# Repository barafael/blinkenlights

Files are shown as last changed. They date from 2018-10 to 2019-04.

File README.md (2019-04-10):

# blinkenlights: Blink lights and control other things, controlled by up to 5 input channels

The purpose of this board is to read some standard RC PWM channels, and switch the output MOSFETs accordingly.
This can be used to blink lights on an RC airplane in patterns, for example. The input channel allows to switch between modes, like standard flying mode and Taxi/Standby modes. Or, a landing light can be switched on/off by a separate channel.
The channels can be either dedicated lines from the receiver, or just other lines which are in use anyway. For example, the throttle signal could be used to switch between standby and flying, and the landing flaps signal could turn on/off the landing lights.

It would be easily possible to dim lights using PWM, I just have not made use of that yet.

The code pretty much just reads the input channels and reads the state from them, and then passes that state (and a tick value) to a function for each output pin. The function can then decide to do whatever with the output pin.

RC PWM signal is read using interrupts, and the program detects when a signal has been disconnected, resetting the state accordingly. That means that you can attach, detach, and reattach PWM signals during operation as you like.

The I2C pins are still free and accessible, so it would be possible to hook up I2C sensors also, like a temperature sensor on the brakes or a barometer.

Input voltage goes directly to the Pro Mini internal regulator, that means it should be 3.3V-16V.

That input voltage is directly supplied to the output pins via the MOSFET driver: an IRLML6244TRPBF SOT-23 package which can switch up to 6.3A (according to datasheet, but I haven't stressed it like that yet).

The PCB is designed in KiCad.

If you have any suggestions or spot an error somewhere, please let me know!

Render of PCB:
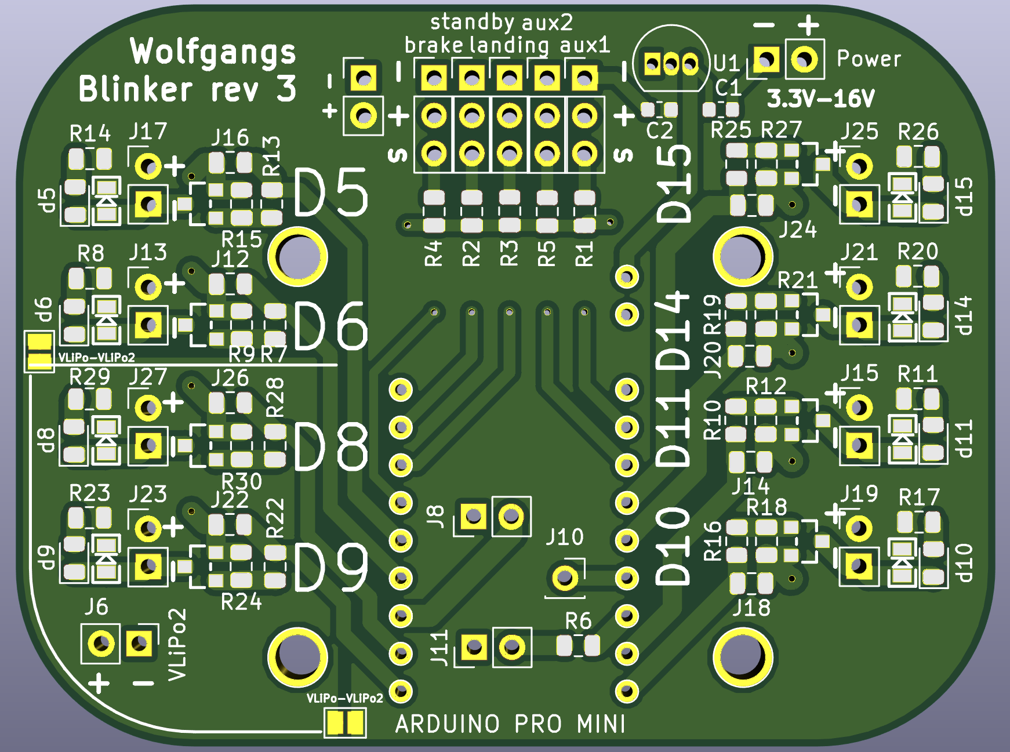
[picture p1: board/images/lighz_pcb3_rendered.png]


PCB in pcbnew:
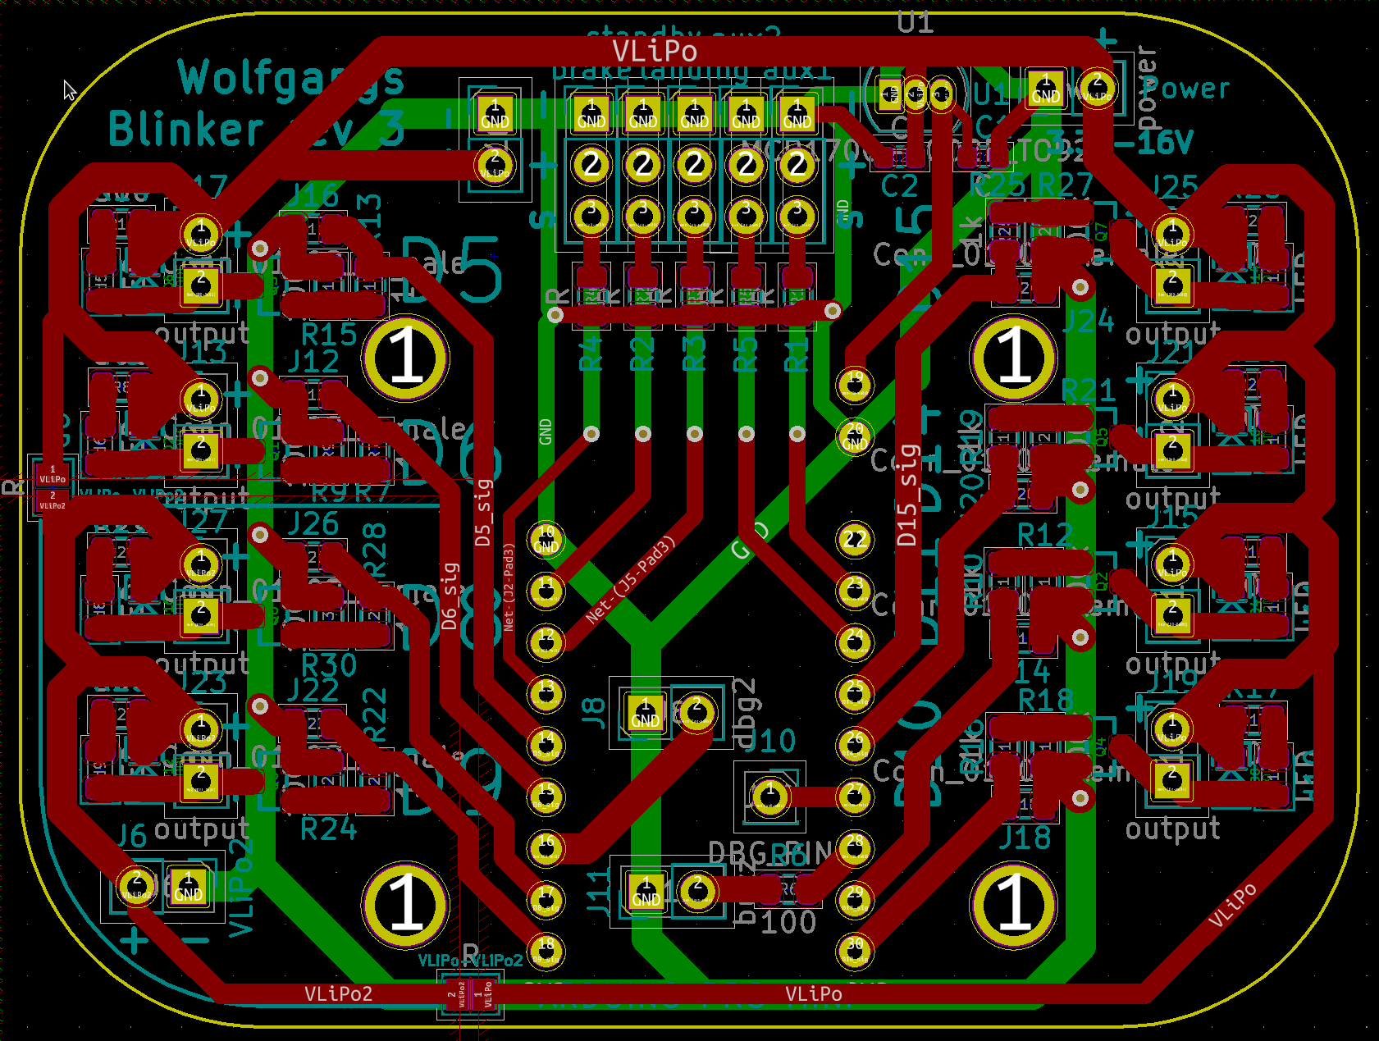
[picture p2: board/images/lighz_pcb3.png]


Schematic:
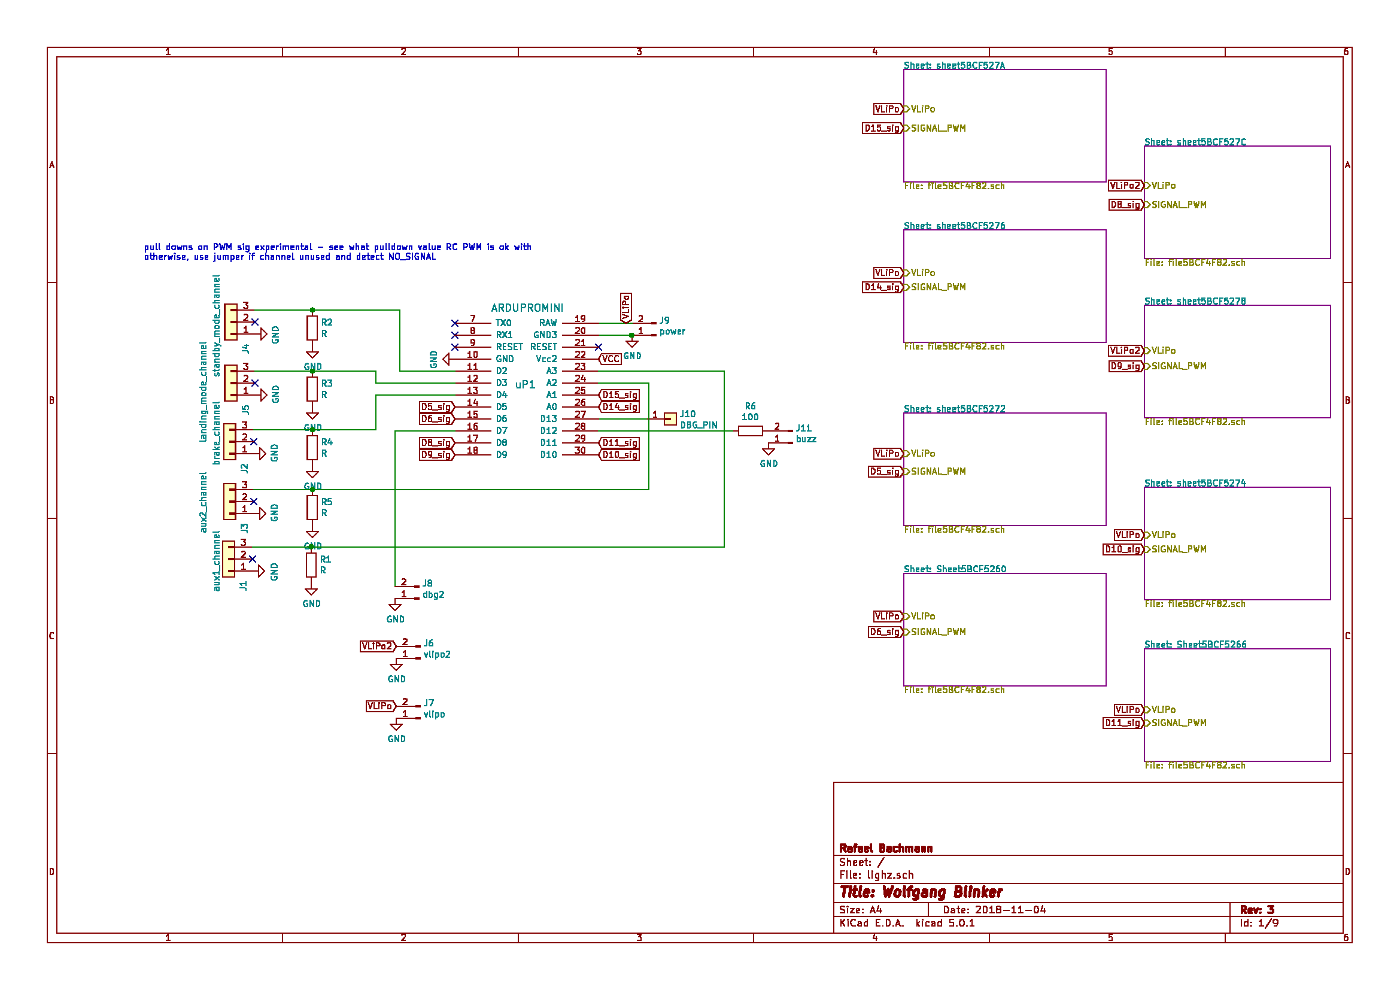
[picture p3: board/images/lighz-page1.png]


MOSFET driver schematic:
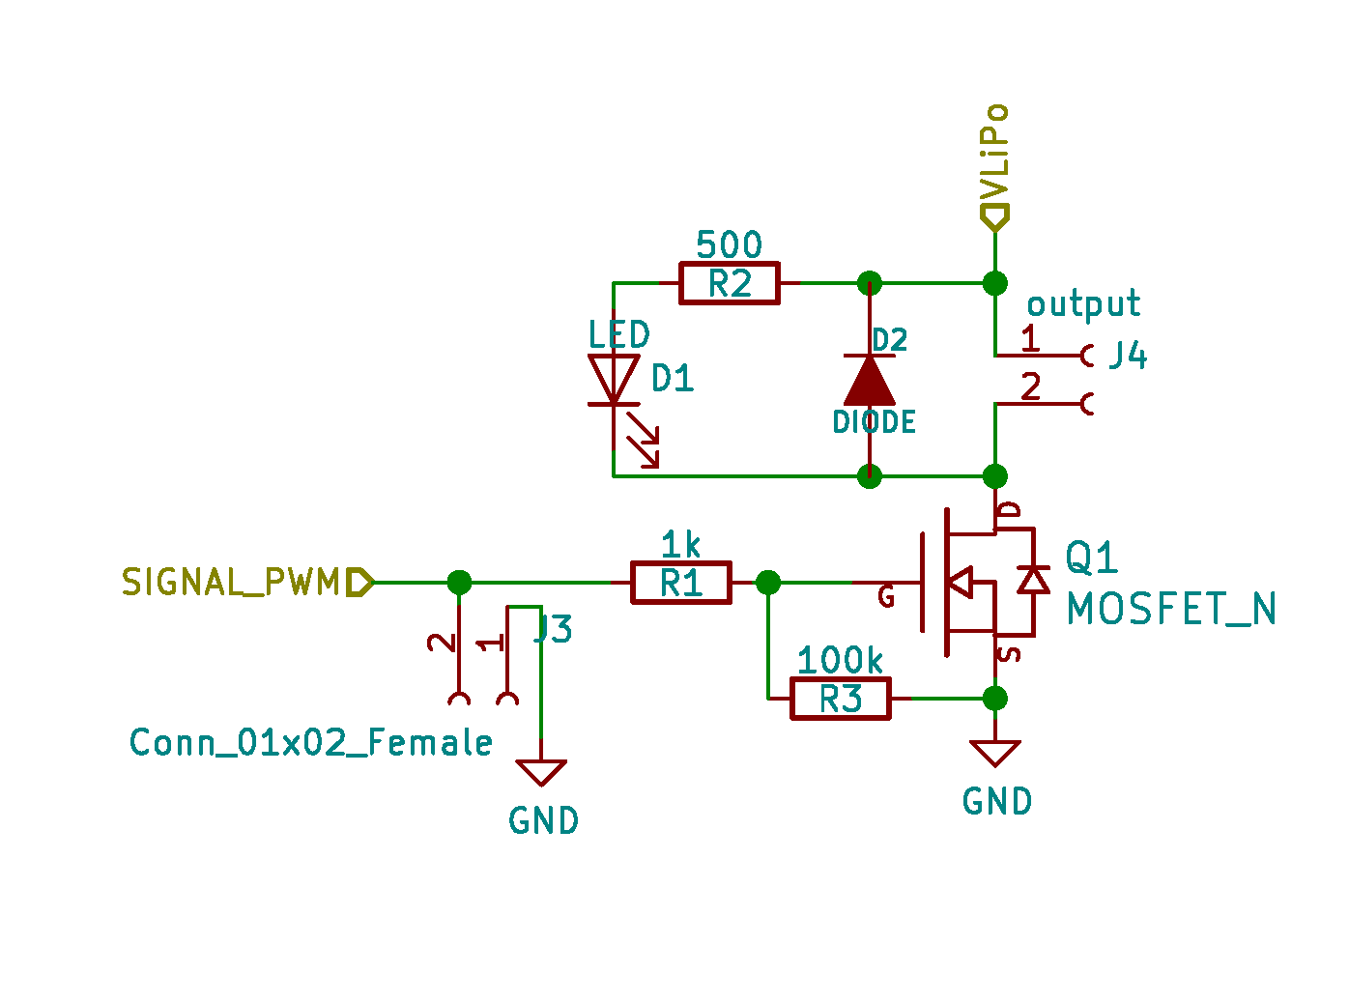
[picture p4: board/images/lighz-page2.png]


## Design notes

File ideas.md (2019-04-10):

stm32f030 board. Run RTOS, threads for each lamp.

each pin has config slot. Config board is extra thing that you can plug in config slot.
Configures:
* N modes: you can select which mode to apply settings to (standby, flying, etc)
* led intensity: PWM value, +/- buttons, 7seg displ?
* pattern button: activate (push down), play pattern on other button, deactivate (release)
* speed: how many seconds per run
* ...

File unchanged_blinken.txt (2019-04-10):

#include <PinChangeInterrupt.h>
#include <PinChangeInterruptBoards.h>
#include <PinChangeInterruptPins.h>
#include <PinChangeInterruptSettings.h>

#include <DigitalIO.h>

static DigitalPin<13> TEST_PIN;

static DigitalPin<5>  D5_PIN;
static DigitalPin<6>  D6_PIN;
static DigitalPin<8>  D8_PIN;
static DigitalPin<9>  D9_PIN;
static DigitalPin<10> D10_PIN;
//static DigitalPin<11> D11_PIN;
static DigitalPin<14> D14_PIN;
static DigitalPin<15> D15_PIN;

static const int BUZZER_PIN = 12;

static DigitalPin<7> DBG_PIN;

/* To enter standby mode, activate landing lights, or enable brakes etc.
   apply an RC PWM signal to these pins */
// Only 2, 3 pins support real interrupts on the pro mini
static const int STANDBY_MODE_CHANNEL_PIN  = 2;
static const int LANDING_LIGHT_CHANNEL_PIN = 3;
static const int BRAKE_CHANNEL_PIN         = 4;
static const int AUX1_CHANNEL_PIN          = A3;
static const int AUX2_CHANNEL_PIN          = A2;

/* These thresholds define when a mode should be active
   (compared against RC PWM value on resp. pin) */
static const uint64_t STANDBY_MODE_THRESHOLD  = 1900;
static const uint64_t LANDING_LIGHT_THRESHOLD = 1800;
static const uint64_t BRAKE_THRESHOLD         = 1500;

/* Counter for main loop,
   subdivides each cycle into MILLISECONDS_PER_CYCLE steps */
static uint64_t counter = 0;

/* The counter runs 0..COUNTER_MAX */
static const uint64_t COUNTER_MAX = 1000;

/* loop wait time MILLISECONDS_PER_STEP is such that one entire counter cycle
   takes MILLISECONDS_PER_CYCLE milliseconds */
static const uint64_t MILLISECONDS_PER_CYCLE = 1200;
static const uint64_t MILLISECONDS_PER_STEP  = MILLISECONDS_PER_CYCLE / COUNTER_MAX;

typedef enum { FLYING, STANDBY } mode_t;

typedef struct {
  mode_t mode;
  /* Flag indicates if landing light should be on */
  bool landing_light_active;
  bool brake_active;
} state_t;

static state_t current_state = { FLYING, false, false };

/* Time in microseconds after which an RC PWM signal is considered stale */
#define PWM_CYCLE_TIMEOUT_MICROS 20000
#define PWM_PULSE_TIMEOUT_MICROS 5000

/* Flag invalid RC PWM pulse signal */
static const uint8_t NO_SIGNAL = 0;

/* Variables to measure pulse duration of RC PWM pulse
   volatile because shared with interrupts */
static volatile uint64_t standby_channel_rise_shared;
static volatile uint64_t standby_channel_pulse_time_shared;

static volatile uint64_t landing_channel_rise_shared;
static volatile uint64_t landing_channel_pulse_time_shared;

static volatile uint64_t brake_channel_rise_shared;
static volatile uint64_t brake_channel_pulse_time_shared;

static volatile uint64_t aux1_channel_rise_shared;
static volatile uint64_t aux1_channel_pulse_time_shared;

static volatile uint64_t aux2_channel_rise_shared;
static volatile uint64_t aux2_channel_pulse_time_shared;

/* Non-volatile, non-shared variables to access pulse time */
static uint64_t standby_channel_pulse_time = NO_SIGNAL;
static uint64_t landing_channel_pulse_time = NO_SIGNAL;
static uint64_t brake_channel_pulse_time   = NO_SIGNAL;
static uint64_t aux1_channel_pulse_time    = NO_SIGNAL;
static uint64_t aux2_channel_pulse_time    = NO_SIGNAL;

static uint64_t standby_channel_rise;
static uint64_t landing_channel_rise;
static uint64_t brake_channel_rise;
static uint64_t aux1_channel_rise;
static uint64_t aux2_channel_rise;

void setup() {
  Serial.begin(250000);

  TEST_PIN.mode(OUTPUT);

  D5_PIN.mode(OUTPUT);
  D6_PIN.mode(OUTPUT);
  D8_PIN.mode(OUTPUT);
  D9_PIN.mode(OUTPUT);
  D10_PIN.mode(OUTPUT);
  //D11_PIN.mode(OUTPUT);
  pinMode(11, OUTPUT);
  D14_PIN.mode(OUTPUT);
  D15_PIN.mode(OUTPUT);

  /* Turn off the lights */
  TEST_PIN.low();

  D5_PIN.low();
  analogWrite(6, 0);
  D8_PIN.low();
  D9_PIN.low();
  analogWrite(10, 0);
  //D11_PIN.low();
  D14_PIN.low();
  D15_PIN.low();

  pinMode(STANDBY_MODE_CHANNEL_PIN,  INPUT);
  pinMode(LANDING_LIGHT_CHANNEL_PIN, INPUT);
  pinMode(BRAKE_CHANNEL_PIN,         INPUT);
  pinMode(AUX1_CHANNEL_PIN,          INPUT);
  pinMode(AUX2_CHANNEL_PIN,          INPUT);

  /* Attach interrupts for pulse time measurement */
  attachInterrupt(digitalPinToInterrupt(STANDBY_MODE_CHANNEL_PIN),  standby_channel_interrupt, CHANGE);
  attachInterrupt(digitalPinToInterrupt(LANDING_LIGHT_CHANNEL_PIN), landing_channel_interrupt, CHANGE);

  /* Use PinChangeInterrupt for pins other than 2, 3 */
  attachPinChangeInterrupt(digitalPinToPinChangeInterrupt(BRAKE_CHANNEL_PIN), brake_channel_interrupt, CHANGE);
  attachPinChangeInterrupt(digitalPinToPinChangeInterrupt(AUX1_CHANNEL_PIN),  aux1_channel_interrupt,  CHANGE);
  attachPinChangeInterrupt(digitalPinToPinChangeInterrupt(AUX2_CHANNEL_PIN),  aux2_channel_interrupt,  CHANGE);

  startup_blink();
  startup_buzz();
}

void startup_blink() {
  TEST_PIN.high();
  delay(50);
  D5_PIN.high();
  delay(50);
  analogWrite(6, 100);
  delay(50);
  D8_PIN.high();
  delay(50);
  D9_PIN.high();
  delay(50);
  analogWrite(10, 100);
  delay(50);
  //D11_PIN.high();
  delay(50);
  D14_PIN.high();
  delay(50);
  D15_PIN.high();
  delay(50);

  TEST_PIN.low();
  D5_PIN.low();
  analogWrite(6, 0);
  D8_PIN.low();
  D9_PIN.low();
  analogWrite(10, 0);
  //D11_PIN.low();
  D14_PIN.low();
  D15_PIN.low();
}

void startup_buzz() {
  tone(BUZZER_PIN, 1245);
  delay(100);
  noTone(BUZZER_PIN);
  tone(BUZZER_PIN, 1319);
  delay(100);
  noTone(BUZZER_PIN);
  tone(BUZZER_PIN, 1568);
  delay(100);
  noTone(BUZZER_PIN);
  tone(BUZZER_PIN, 1976);
  delay(100);
  noTone(BUZZER_PIN);
  tone(BUZZER_PIN, 2349);
  delay(200);
  noTone(BUZZER_PIN);
  tone(BUZZER_PIN, 2093);
  delay(100);
  noTone(BUZZER_PIN);
  tone(BUZZER_PIN, 1568);
  delay(200);
  noTone(BUZZER_PIN);
  tone(BUZZER_PIN, 1319);
  delay(100);
  noTone(BUZZER_PIN);
  tone(BUZZER_PIN, 2349);
  delay(200);
  noTone(BUZZER_PIN);
  tone(BUZZER_PIN, 2093);
  delay(400);
  noTone(BUZZER_PIN);
}

void loop() {
  uint64_t loop_start_millis = millis();

  /* Handle RC PWM input */
  {
    /* Copy over shared volatile variables */
    noInterrupts();
    standby_channel_pulse_time = standby_channel_pulse_time_shared;
    landing_channel_pulse_time = landing_channel_pulse_time_shared;
    brake_channel_pulse_time   = brake_channel_pulse_time_shared;
    aux1_channel_pulse_time    = aux1_channel_pulse_time_shared;
    aux2_channel_pulse_time    = aux2_channel_pulse_time_shared;

    standby_channel_rise = standby_channel_rise_shared;
    landing_channel_rise = landing_channel_rise_shared;
    brake_channel_rise   = brake_channel_rise_shared;
    aux1_channel_rise    = aux1_channel_rise_shared;
    aux2_channel_rise    = aux2_channel_rise_shared;
    interrupts();

    /* Check for stale pulse time readings */
    const uint64_t now = micros();
    if ((now - standby_channel_rise) > PWM_CYCLE_TIMEOUT_MICROS ||
        standby_channel_pulse_time > PWM_PULSE_TIMEOUT_MICROS) {
      // ignoring interrupt here, assumption is that it won't been triggered
      // since that has not happened for PWM_CYCLE_TIMEOUT_MICROS microseconds
      standby_channel_pulse_time        = NO_SIGNAL;
      standby_channel_pulse_time_shared = NO_SIGNAL;
    }
    if ((now - landing_channel_rise) > PWM_CYCLE_TIMEOUT_MICROS ||
        landing_channel_pulse_time > PWM_PULSE_TIMEOUT_MICROS) {
      // ignoring interrupt here, assumption is that it won't been triggered
      // since that has not happened for PWM_CYCLE_TIMEOUT_MICROS microseconds
      landing_channel_pulse_time        = NO_SIGNAL;
      landing_channel_pulse_time_shared = NO_SIGNAL;
    }
    if ((now - brake_channel_rise) > PWM_CYCLE_TIMEOUT_MICROS ||
        brake_channel_pulse_time > PWM_PULSE_TIMEOUT_MICROS) {
      // ignoring interrupt here, assumption is that it won't been triggered
      // since that has not happened for PWM_CYCLE_TIMEOUT_MICROS microseconds
      brake_channel_pulse_time        = NO_SIGNAL;
      brake_channel_pulse_time_shared = NO_SIGNAL;
    }
    if ((now - aux1_channel_rise) > PWM_CYCLE_TIMEOUT_MICROS ||
        aux1_channel_pulse_time > PWM_PULSE_TIMEOUT_MICROS) {
      // ignoring interrupt here, assumption is that it won't been triggered
      // since that has not happened for PWM_CYCLE_TIMEOUT_MICROS microseconds
      aux1_channel_pulse_time        = NO_SIGNAL;
      aux1_channel_pulse_time_shared = NO_SIGNAL;
    }
    if ((now - aux2_channel_rise) > PWM_CYCLE_TIMEOUT_MICROS ||
        aux2_channel_pulse_time > PWM_PULSE_TIMEOUT_MICROS) {
      // ignoring interrupt here, assumption is that it won't been triggered
      // since that has not happened for PWM_CYCLE_TIMEOUT_MICROS microseconds
      aux2_channel_pulse_time        = NO_SIGNAL;
      aux2_channel_pulse_time_shared = NO_SIGNAL;
    }
  }

  /* Read if signal present */
  bool standby_mode_enabled  = standby_channel_pulse_time != NO_SIGNAL;
  bool landing_light_enabled = landing_channel_pulse_time != NO_SIGNAL;

  /* Set mode to standby only if mode is enabled */
  if (standby_mode_enabled) {
    if (standby_channel_pulse_time < STANDBY_MODE_THRESHOLD) {
      current_state.mode = STANDBY;
    } else {
      current_state.mode = FLYING;
    }
  } else {
    /* If mode not enabled, state is FLYING */
    current_state.mode = FLYING;
  }

  if (landing_light_enabled) {
    current_state.landing_light_active = landing_channel_pulse_time < LANDING_LIGHT_THRESHOLD;
  } else {
    current_state.landing_light_active = false;
  }

  if (brake_channel_pulse_time > BRAKE_THRESHOLD) {
    current_state.brake_active = true;
  } else {
    current_state.brake_active = false;
  }

  /* Update outputs with current state */
  update_test_pin(counter, &current_state);

  updateOutput_D5(counter,  &current_state);
  updateOutput_D6(counter,  &current_state);
  updateOutput_D8(counter,  &current_state);
  updateOutput_D9(counter,  &current_state);
  updateOutput_D10(counter, &current_state);
  updateOutput_D11(counter, &current_state);
  updateOutput_D14(counter, &current_state);
  updateOutput_D15(counter, &current_state);

  /* Advance counter */
  if (counter < COUNTER_MAX) {
    counter++;
  } else {
    counter = 0;
  }

  //#define DEBUG_PRINT
#ifdef DEBUG_PRINT
  Serial.print("Counter: ");
  Serial.print((long) counter);
  Serial.print("\t");
  Serial.print("Standby channel: ");
  Serial.print((long) standby_channel_pulse_time);
  Serial.print("\t");
  Serial.print("Landing channel: ");
  Serial.print((long) landing_channel_pulse_time);
  Serial.print("\t");
  Serial.print("Brake channel: ");
  Serial.print((long) brake_channel_pulse_time);
  Serial.print("\t");
  Serial.print("AUX1 channel: ");
  Serial.print((long) aux1_channel_pulse_time);
  Serial.print("\t");
  Serial.print("AUX2 channel: ");
  Serial.print((long) aux2_channel_pulse_time);
  Serial.println();
#endif

  /* Block until MILLISECONDS_PER_STEP have passed */
  while ((millis() - loop_start_millis) < MILLISECONDS_PER_STEP);
}

/* A macro to statically compute a fraction of the steps for a complete cycle.
   By computing the fraction this way, a blink pattern code is independent of the
   number of steps per cycle. */
#define cycle_fraction(a, b) (int) (((double) (a) / (double) (b)) * COUNTER_MAX)

/* Update outputs */
static void update_test_pin(uint64_t tick, state_t *state) {
  switch (state->mode) {
    case FLYING:
      switch (tick) {
        case 0: TEST_PIN.high(); break;
        case cycle_fraction(4, 10): TEST_PIN.low();  break;
        case cycle_fraction(5, 10): TEST_PIN.high(); break;
        case cycle_fraction(9, 10): TEST_PIN.low();  break;
      }
      break;
    case STANDBY:
      switch (tick) {
        case 0: TEST_PIN.high(); break ;
        case cycle_fraction(1, 10):    TEST_PIN.low();  break;
        case cycle_fraction(2, 10):    TEST_PIN.high(); break;
        case cycle_fraction(3, 10):    TEST_PIN.low();  break;
        case cycle_fraction(9, 10):    TEST_PIN.high(); break;
        case cycle_fraction(9.25, 10): TEST_PIN.low();  break ;
      }
      break;
  }
}

static void updateOutput_D5(uint64_t tick, state_t *state) {
  if (state->mode == FLYING) {
    switch (tick) {
      case cycle_fraction(0, 10):  D5_PIN.high(); break;
      case cycle_fraction(1, 10):   D5_PIN.low();  break;
      case cycle_fraction(2, 10):  D5_PIN.high(); break;
      case cycle_fraction(3, 10):   D5_PIN.low();  break;
    }
  }
}

static void updateOutput_D6(uint64_t tick, state_t *state) {
  if (state->mode == FLYING) {
    switch (tick) {
      case cycle_fraction(0, 40):   analogWrite(6, 100); break;
      case cycle_fraction(1, 40):   analogWrite(6, 0);  break;
      case cycle_fraction(4, 40):   analogWrite(6, 100);  break;
      case cycle_fraction(5, 40):   analogWrite(6, 0);  break;
      case cycle_fraction(6, 40):   analogWrite(6, 100);  break;
      case cycle_fraction(7, 40):   analogWrite(6, 0);  break;
      case cycle_fraction(8, 40):   analogWrite(6, 100);  break;
      case cycle_fraction(9, 40):   analogWrite(6, 0);  break;
      case cycle_fraction(10, 40):   analogWrite(6, 100);  break;
      case cycle_fraction(11, 40):   analogWrite(6, 0);  break;
    }
  } else if (state->mode == STANDBY) {
    switch (tick) {
      case 0:       analogWrite(6, 100); break;
      case cycle_fraction(1, 2):   analogWrite(6, 0);  break;
    }
  }
}

static void updateOutput_D8(uint64_t tick, state_t *state) {
  if (state->landing_light_active) {
    D8_PIN.high();
  } else {
    D8_PIN.low();
  }
}

static void updateOutput_D9(uint64_t tick, state_t *state) {
  if (state->landing_light_active) {
    D9_PIN.high();
  } else {
    D9_PIN.low();
  }
}

static void updateOutput_D10(uint64_t tick, state_t *state) {
  switch (tick) {
    case 0: analogWrite(10, 0); break;
    case cycle_fraction(8,  20): analogWrite(10, 100);  break;
    case cycle_fraction(9,  20): analogWrite(10, 0); break;
    case cycle_fraction(10, 20): analogWrite(10, 100);  break;
    case cycle_fraction(11, 20): analogWrite(10, 0); break;
  }
}

static void updateOutput_D11(uint64_t tick, state_t *state) {
  if (state->landing_light_active) {
    analogWrite(11, 100);
    //D11_PIN.high();
  } else {
    //D11_PIN.low();
    analogWrite(11, 0);
  }
}

static void updateOutput_D14(uint64_t tick, state_t *state) {
  if (state->mode == FLYING) {
    switch (tick) {
      case cycle_fraction(0,  4): D14_PIN.low(); break;
      case cycle_fraction(3,  4): D14_PIN.high();  break;
      case cycle_fraction(31, 40): D14_PIN.low(); break;
      case cycle_fraction(33, 40): D14_PIN.high();  break;
      case cycle_fraction(34, 40): D14_PIN.low();  break;
    }
  }
}

static void updateOutput_D15(uint64_t tick, state_t *state) {
  if (state->mode == FLYING) {
    switch (tick) {
      case cycle_fraction(5, 10):  D15_PIN.high(); break;
      case cycle_fraction(6, 10):  D15_PIN.low();  break;
      case cycle_fraction(7, 10):  D15_PIN.high(); break;
      case cycle_fraction(8, 10):  D15_PIN.low();  break;
    }
  } else if (state->mode == STANDBY) {
    switch (tick) {
      case 0: D15_PIN.low(); break;
    }
  }
}

/* RC PWM input handling functions */
static void standby_channel_interrupt() {
  if (digitalRead(STANDBY_MODE_CHANNEL_PIN) == HIGH) {
    standby_channel_rise_shared = micros();
  } else {
    standby_channel_pulse_time_shared = micros() - standby_channel_rise_shared;
  }
}

static void landing_channel_interrupt() {
  if (digitalRead(LANDING_LIGHT_CHANNEL_PIN) == HIGH) {
    landing_channel_rise_shared = micros();
  } else {
    landing_channel_pulse_time_shared = micros() - landing_channel_rise_shared;
  }
}

static void brake_channel_interrupt() {
  uint8_t trigger = getPinChangeInterruptTrigger(digitalPinToPCINT(BRAKE_CHANNEL_PIN));
  if (trigger == RISING) {
    brake_channel_rise_shared = micros();
  } else if (trigger == FALLING) {
    brake_channel_pulse_time_shared = micros() - brake_channel_rise_shared;
  }
}

static void aux1_channel_interrupt() {
  uint8_t trigger = getPinChangeInterruptTrigger(digitalPinToPCINT(AUX1_CHANNEL_PIN));
  if (trigger == RISING) {
    aux1_channel_rise_shared = micros();
  } else if (trigger == FALLING) {
    aux1_channel_pulse_time_shared = micros() - aux1_channel_rise_shared;
  }
}

static void aux2_channel_interrupt() {
  uint8_t trigger = getPinChangeInterruptTrigger(digitalPinToPCINT(AUX2_CHANNEL_PIN));
  if (trigger == RISING) {
    aux2_channel_rise_shared = micros();
  } else if (trigger == FALLING) {
    aux2_channel_pulse_time_shared = micros() - aux2_channel_rise_shared;
  }
}

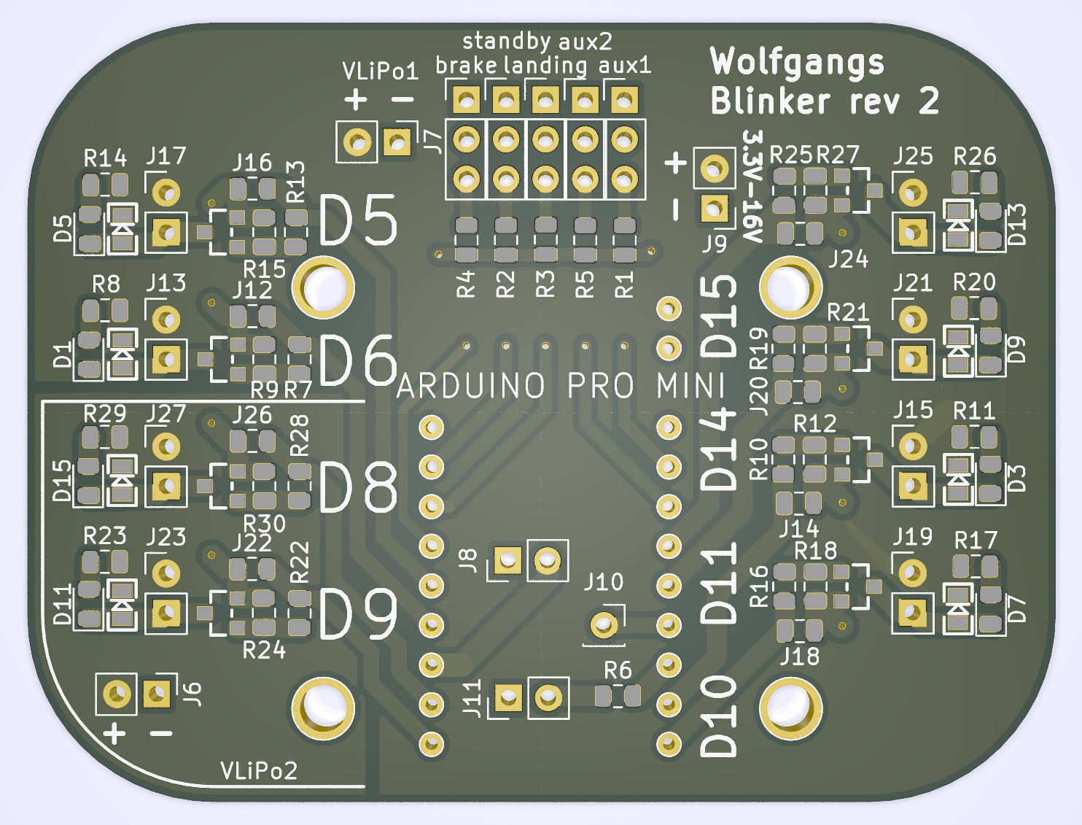
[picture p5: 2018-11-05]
board/images/lighz_pcb2_rendered.png

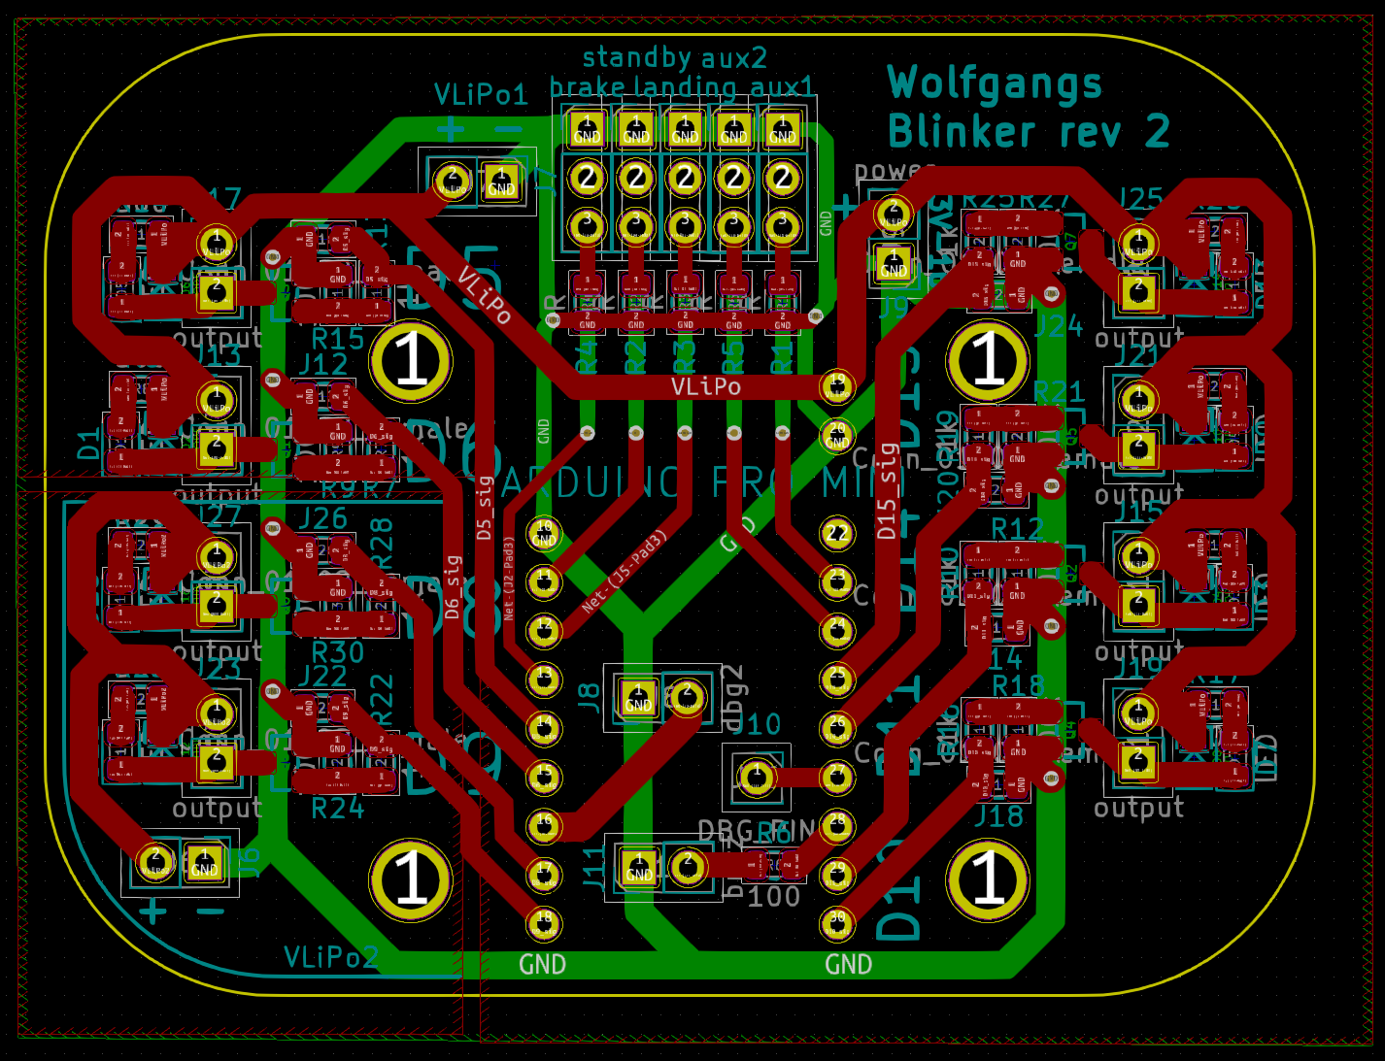
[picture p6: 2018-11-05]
board/images/lighz_pcb2.png

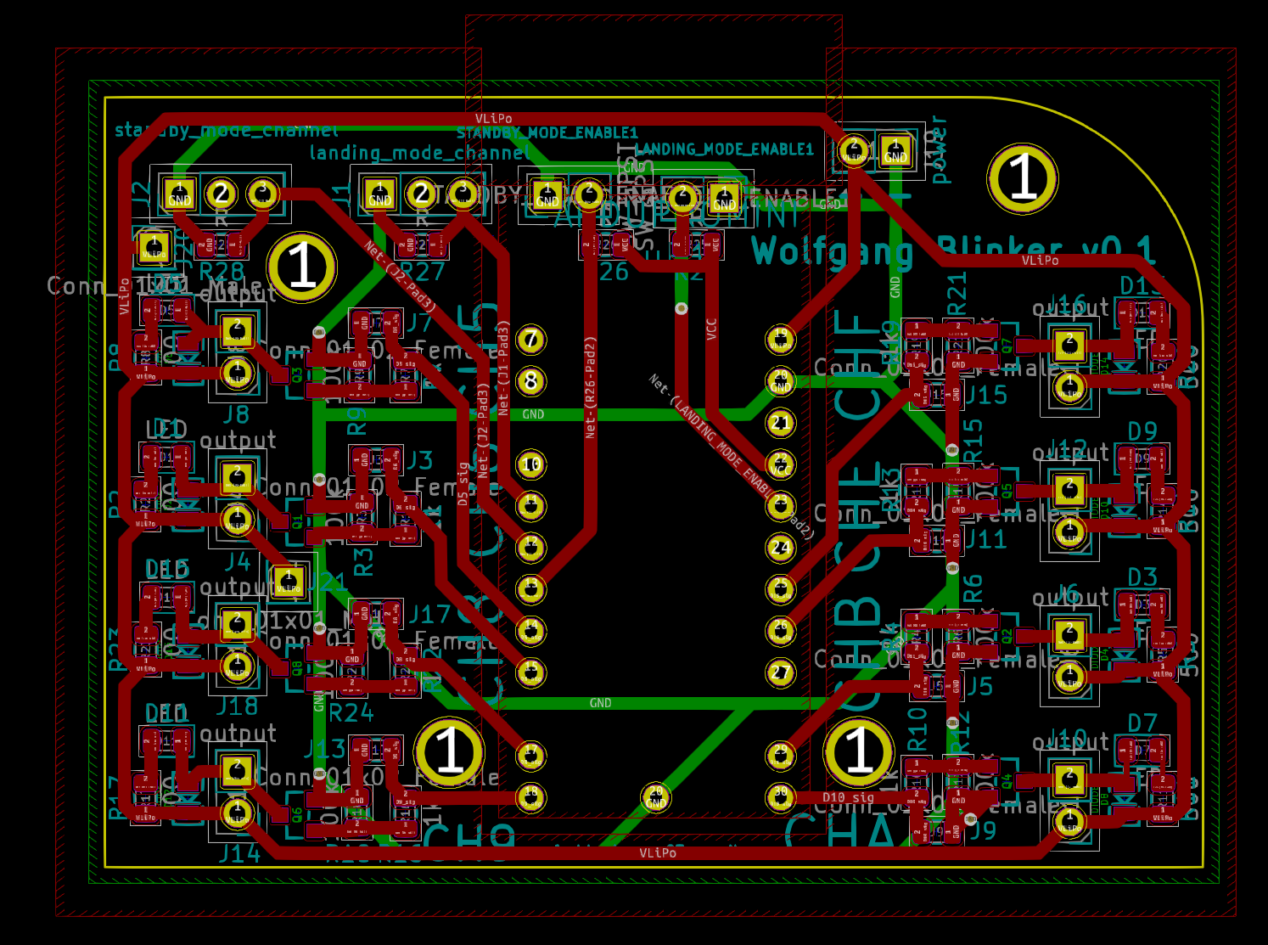
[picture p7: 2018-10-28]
board/images/lighz_pcb.png

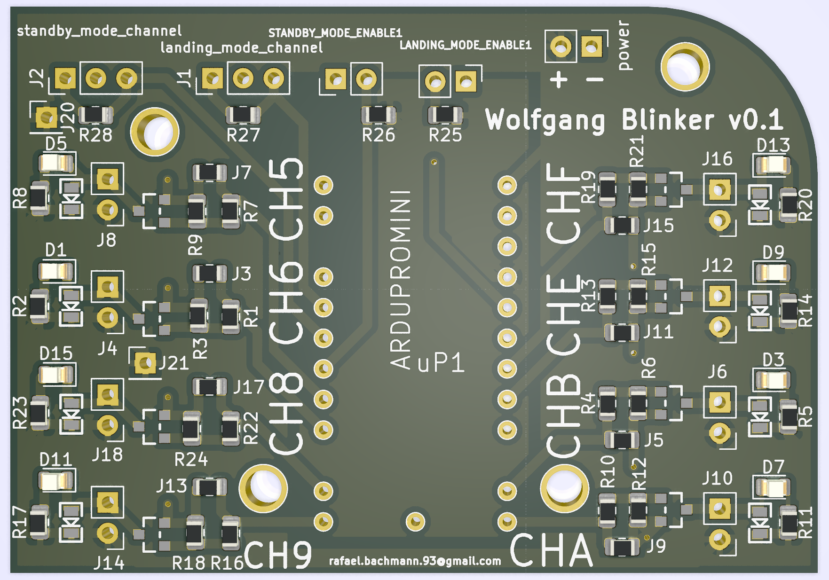
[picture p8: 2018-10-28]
board/images/lighz_pcb_rendered.png

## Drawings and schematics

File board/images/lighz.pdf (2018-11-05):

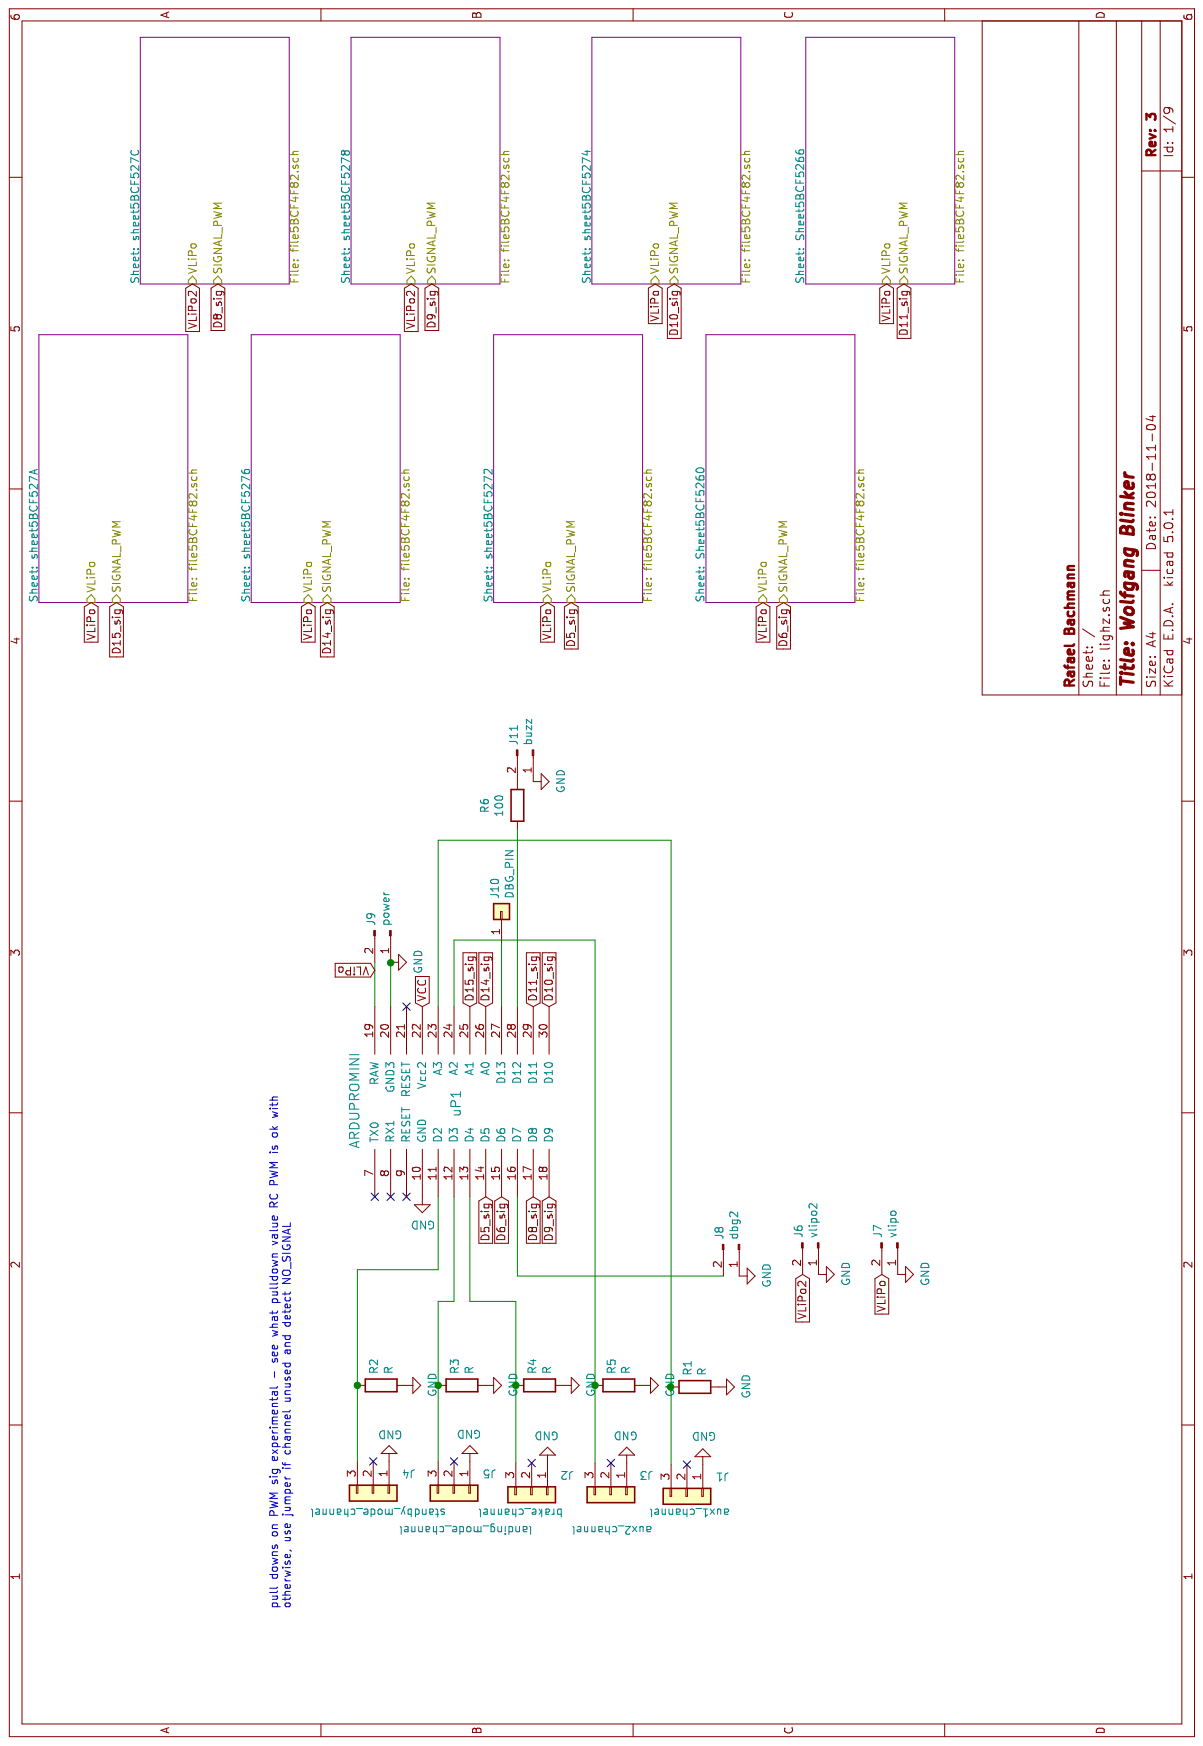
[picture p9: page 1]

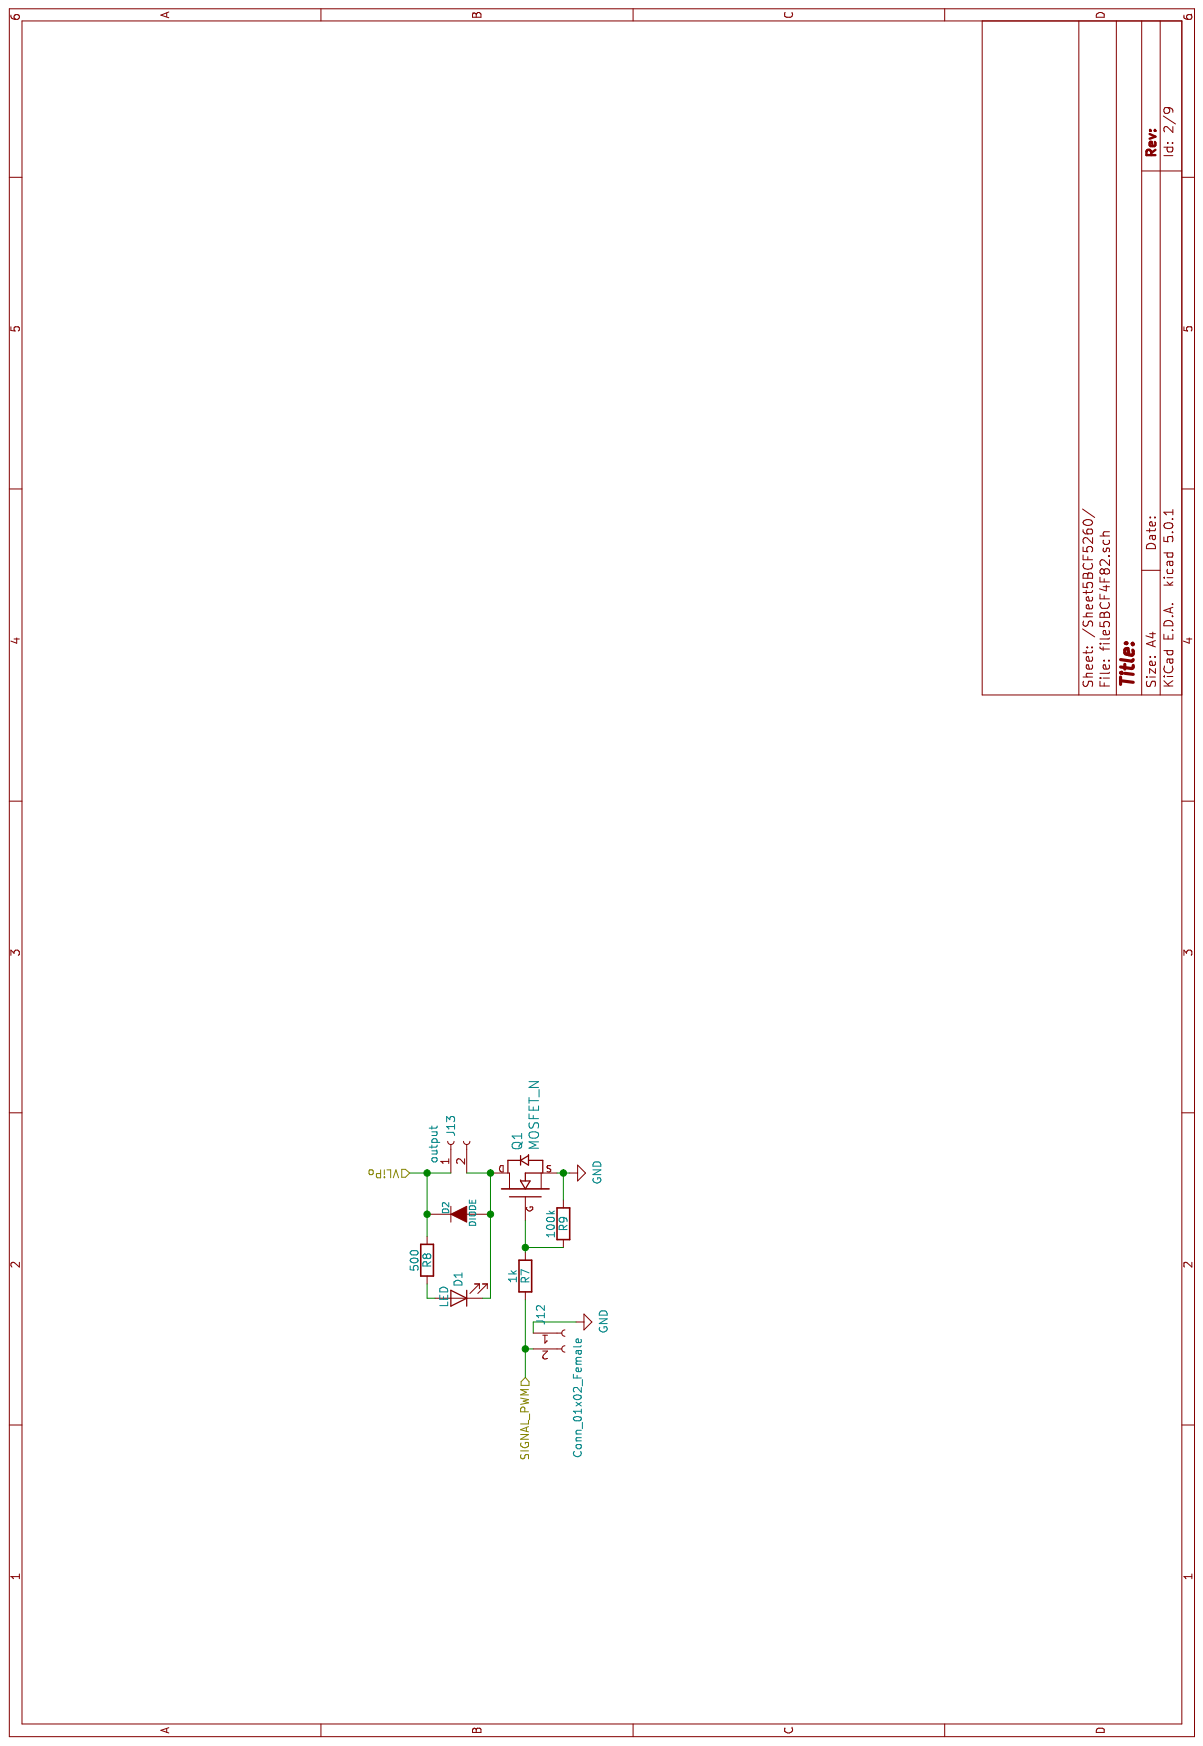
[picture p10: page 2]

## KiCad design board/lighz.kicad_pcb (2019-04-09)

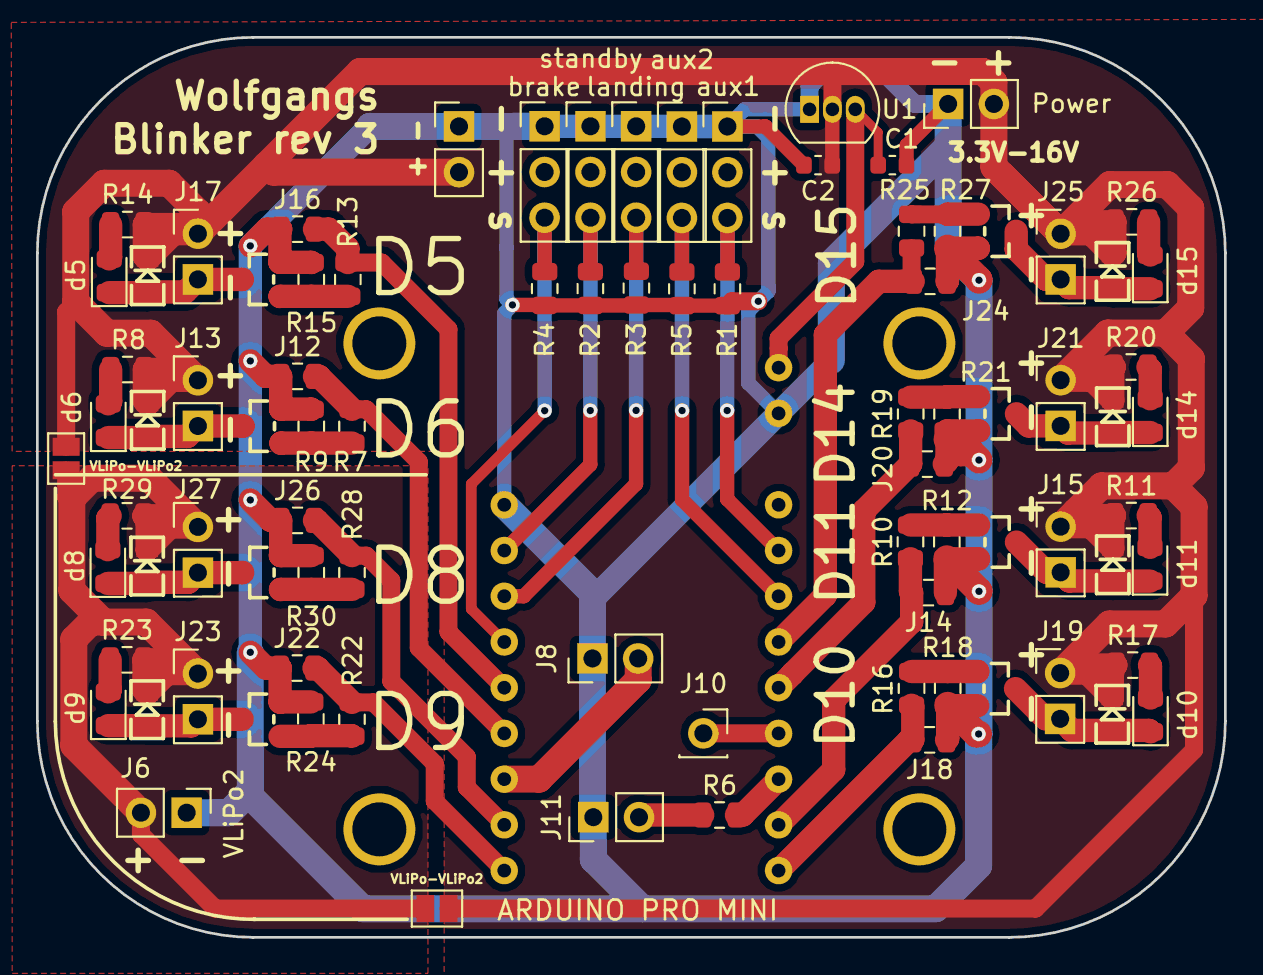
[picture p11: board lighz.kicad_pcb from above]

Board: 2 copper layers, 66.0 x 50.0 mm, 91 parts (0 on the bottom side), 45 nets.

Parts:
1pin_prototyping, 1pin_prototyping#2, 1pin_prototyping#3, 1pin_prototyping#4: val**; 1pin_prototyping
C1, C2: C; C_0603_1608Metric
D2, D4, D6, D8, D10, D12, D14, D16: DIODE; LED-0805
J1: aux1; PinHeader_1x03_P2.54mm_Vertical
J2: brake; PinHeader_1x03_P2.54mm_Vertical
J3: aux2; PinHeader_1x03_P2.54mm_Vertical
J4: standby; PinHeader_1x03_P2.54mm_Vertical
J5: landing; PinHeader_1x03_P2.54mm_Vertical
J6: VLiPo2; PinHeader_1x02_P2.54mm_Vertical
J7: vlipo; PinHeader_1x02_P2.54mm_Vertical
J8: dbg2; PinHeader_1x02_P2.54mm_Vertical
J10: DBG_PIN; PinSocket_1x01_P2.54mm_Vertical
J11: buzz; PinHeader_1x02_P2.54mm_Vertical
J12, J14, J16, J18, J20, J22, J24, J26: Conn_01x02_Female; R_0805_2012Metric
J13, J15, J17, J19, J21, J23, J25, J27: output; PinHeader_1x02_P2.54mm_Vertical
Power: power; PinHeader_1x02_P2.54mm_Vertical
Q1, Q2, Q3, Q4, Q5, Q6, Q7, Q8: MOSFET_N; SOT23_FET
R1, R2, R3, R4, R5: R; R_0805_2012Metric
R6: 100; R_0805_2012Metric
R7, R10, R13, R16, R19, R22, R25, R28: 1k; R_0805_2012Metric
R8, R11, R14, R17, R20, R23, R26, R29: 500; R_0805_2012Metric
R9, R12, R15, R18, R21, R24, R27, R30: 100k; R_0805_2012Metric
U1: MCP1700-5002E_TO92; TO-92_Inline
VLiPo-VLiPo2, VLiPo-VLiPo2#2: R; SolderJumper-2_P1.3mm_Open_Pad1.0x1.5mm
d5, d6, d8, d9, d10, d11, d14, d15: LED; LED_0805_2012Metric
uP1: ARDUINO PRO MINI; ArduProMini-6

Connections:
D5_sig: J16.2, R13.2, uP1.14
D6_sig: J12.2, R7.2, uP1.15
D8_sig: J26.2, R28.2, uP1.17
D9_sig: J22.2, R22.2, uP1.18
D10_sig: J18.2, R16.2, uP1.30
D11_sig: J14.2, R10.2, uP1.29
D14_sig: J20.2, R19.2, uP1.26
D15_sig: J24.2, R25.2, uP1.25
GND: C1.2, C2.2, J1.1, J2.1, J3.1, J4.1, J5.1, J6.1, J7.1, J8.1, J11.1, J12.1, J14.1, J16.1, J18.1, J20.1, J22.1, J24.1, J26.1, Power.1, Q1.S, Q2.S, Q3.S, Q4.S, Q5.S, Q6.S, Q7.S, Q8.S, R1.2, R2.2, R3.2, R4.2, R5.2, R9.1, R12.1, R15.1, R18.1, R21.1, R24.1, R27.1, R30.1, U1.1, uP1.10, uP1.20
unnamed: C1.1, U1.3, uP1.19
unnamed: D2.A, J13.2, Q1.D, d6.1
unnamed: R8.2, d6.2
unnamed: D4.A, J15.2, Q2.D, d11.1
unnamed: R11.2, d11.2
unnamed: D6.A, J17.2, Q3.D, d5.1
unnamed: R14.2, d5.2
unnamed: D8.A, J19.2, Q4.D, d10.1
unnamed: R17.2, d10.2
unnamed: R20.2, d14.2
unnamed: D10.A, J21.2, Q5.D, d14.1
unnamed: D12.A, J23.2, Q6.D, d9.1
unnamed: R23.2, d9.2
unnamed: D14.A, J25.2, Q7.D, d15.1
unnamed: R26.2, d15.2
unnamed: D16.A, J27.2, Q8.D, d8.1
unnamed: R29.2, d8.2
unnamed: J1.3, R1.1, uP1.23
unnamed: J2.3, R4.1, uP1.13
unnamed: J3.3, R5.1, uP1.24
unnamed: J4.3, R2.1, uP1.11
unnamed: J5.3, R3.1, uP1.12
unnamed: J8.2, uP1.16
unnamed: J10.1, uP1.27
unnamed: J11.2, R6.1
unnamed: Q1.G, R7.1, R9.2
unnamed: Q2.G, R10.1, R12.2
unnamed: Q3.G, R13.1, R15.2
unnamed: Q4.G, R16.1, R18.2
unnamed: Q5.G, R19.1, R21.2
unnamed: Q6.G, R22.1, R24.2
unnamed: Q7.G, R25.1, R27.2
unnamed: Q8.G, R28.1, R30.2
unnamed: R6.2, uP1.28
VLiPo: C2.1, D2.K, D4.K, D6.K, D8.K, D10.K, D14.K, J7.2, J13.1, J15.1, J17.1, J19.1, J21.1, J25.1, Power.2, R8.1, R11.1, R14.1, R17.1, R20.1, R26.1, U1.2, VLiPo-VLiPo2.1, VLiPo-VLiPo2#2.1
VLiPo2: D12.K, D16.K, J6.2, J23.1, J27.1, R23.1, R29.1, VLiPo-VLiPo2.2, VLiPo-VLiPo2#2.2

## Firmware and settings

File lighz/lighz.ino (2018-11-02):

#include <DigitalIO.h>

static const DigitalPin<13> TEST_PIN;

static const DigitalPin<5>  D5_PIN;
static const DigitalPin<6>  D6_PIN;
static const DigitalPin<8>  D8_PIN;
static const DigitalPin<9>  D9_PIN;
static const DigitalPin<10> D10_PIN;
static const DigitalPin<11> D11_PIN;
static const DigitalPin<14> D14_PIN;
static const DigitalPin<15> D15_PIN;

/* standby blinking and landing lights are optional features.
   They can be set by jumpers on these pins */
static const int STANDBY_MODE_ENABLE_PIN  = 4;
static const int LANDING_LIGHT_ENABLE_PIN = A3;

/* To enter standby mode or activate landing lights,
   apply an RC PWM signal to these pinns */
// Only these two pins support real interrupts on the pro mini
static const int STANDBY_MODE_CHANNEL_PIN  = 2;
static const int LANDING_LIGHT_CHANNEL_PIN = 3;

/* These thresholds define when a mode should be active
   (compared against RC PWM value on resp. pin) */
static const uint64_t STANDBY_MODE_THRESHOLD  = 1500;
static const uint64_t LANDING_LIGHT_THRESHOLD = 1500;

/* standby mode and landing light feature enabled-ness */
static bool standby_mode_enabled  = false;
static bool landing_light_enabled = false;

/* Counter for main loop,
   subdivides each cycle into MILLISECONDS_PER_CYCLE steps*/
static uint64_t counter = 0;

/* The counter runs 0..COUNTER_MAX */
static const uint64_t COUNTER_MAX = 1000;

/* loop wait time MILLISECONDS_PER_STEP is such that one entire counter cycle
   takes MILLISECONDS_PER_CYCLE milliseconds */
static const uint64_t MILLISECONDS_PER_CYCLE = 3000;
static const uint64_t MILLISECONDS_PER_STEP  = MILLISECONDS_PER_CYCLE / COUNTER_MAX;

/* If standby_mode_enabled:
       if threshold condition is met, enter STANDBY mode
   else:
       enter FLYING mode
   If landing_light_enabled:
       if  threshold condition is met, turn on lights
   else:
       lights off
*/
typedef enum { FLYING, STANDBY } flying_state_t;

typedef struct {
    flying_state_t fly_state;
    /* Flag indicates if landing light should be on */
    bool landing_light_active;
} state_t;

static state_t current_state = { STANDBY, false };

/* Variables to measure pulse duration of RC PWM pulse
   volatile because shared with interrupts */
static volatile uint64_t standby_channel_rise;
static volatile uint64_t standby_channel_pulse_time;
static volatile uint64_t landing_channel_rise;
static volatile uint64_t landing_channel_pulse_time;

void setup() {
    Serial.begin(250000);

    TEST_PIN.mode(OUTPUT);

    D5_PIN.mode (OUTPUT);
    D6_PIN.mode (OUTPUT);
    D8_PIN.mode (OUTPUT);
    D9_PIN.mode (OUTPUT);
    D10_PIN.mode(OUTPUT);
    D11_PIN.mode(OUTPUT);
    D14_PIN.mode(OUTPUT);
    D15_PIN.mode(OUTPUT);

    /* Turn off the lights */
    TEST_PIN.low();

    D5_PIN. low();
    D6_PIN. low();
    D8_PIN. low();
    D9_PIN. low();
    D10_PIN.low();
    D11_PIN.low();
    D14_PIN.low();
    D15_PIN.low();

    pinMode(STANDBY_MODE_ENABLE_PIN,  INPUT);
    pinMode(LANDING_LIGHT_ENABLE_PIN, INPUT);

    pinMode(STANDBY_MODE_CHANNEL_PIN,  INPUT);
    pinMode(LANDING_LIGHT_CHANNEL_PIN, INPUT);

    /* attach interrupts even if modes are not enabled right now */
    attachInterrupt(digitalPinToInterrupt(STANDBY_MODE_CHANNEL_PIN), standby_channel_interrupt, CHANGE);
    attachInterrupt(digitalPinToInterrupt(LANDING_LIGHT_CHANNEL_PIN), landing_channel_interrupt, CHANGE);
}

void loop() {
    /* Read if jumpers present (active low) */
    standby_mode_enabled  = digitalRead(STANDBY_MODE_ENABLE_PIN)  == LOW;
    landing_light_enabled = digitalRead(LANDING_LIGHT_ENABLE_PIN) == LOW;

    /* Set mode to standby only if mode is enabled */
    if (standby_mode_enabled) {
        if (standby_channel_pulse_time < STANDBY_MODE_THRESHOLD) {
            current_state.fly_state = STANDBY;
        } else {
            current_state.fly_state = FLYING;
        }
    } else {
        /* If mode not enabled, state is FLYING */
        current_state.fly_state = FLYING;
    }

    if (landing_light_enabled) {
        current_state.landing_light_active =
            landing_channel_pulse_time < LANDING_LIGHT_THRESHOLD;
    } else {
        current_state.landing_light_active = false;
    }

    update_test_pin (counter, current_state);

    updateOutput_D5 (counter, current_state);
    updateOutput_D6 (counter, current_state);
    updateOutput_D8 (counter, current_state);
    updateOutput_D9 (counter, current_state);
    updateOutput_D10(counter, current_state);
    updateOutput_D11(counter, current_state);
    updateOutput_D14(counter, current_state);
    updateOutput_D15(counter, current_state);

    if (counter < COUNTER_MAX) {
        counter++;
    } else {
        counter = 0;
    }

    delay(MILLISECONDS_PER_STEP);

//#define DEBUG_PRINT
#ifdef DEBUG_PRINT
    Serial.print("Counter: ");
    Serial.print((long)counter);
    Serial.print("\t");
    Serial.print("Standby channel: ");
    Serial.print((long)standby_channel_pulse_time);
    Serial.print("\t");
    Serial.print("Landing channel: ");
    Serial.print((long)landing_channel_pulse_time);
    Serial.println("\t");
#endif
}

#define cycle_fraction(a, b) \
    (int)(((double)(a)/(double)(b)) * COUNTER_MAX)

static void update_test_pin(uint64_t tick, state_t state) {
    switch(state.fly_state) {
    case FLYING:
        switch(tick) {
        case 0:
            TEST_PIN.high();
            break;
        case cycle_fraction(4, 10):
            TEST_PIN.low();
            break;
        case cycle_fraction(5, 10):
            TEST_PIN.high();
            break;
        case cycle_fraction(9, 10):
            TEST_PIN.low();
            break;
        }
        break;
    case STANDBY:
        switch(tick) {
        case 0:
            TEST_PIN.high();
            break;
        case cycle_fraction(1, 10):
            TEST_PIN.low();
            break;
        case cycle_fraction(2, 10):
            TEST_PIN.high();
            break;
        case cycle_fraction(3, 10):
            TEST_PIN.low();
            break;
        case cycle_fraction(9, 10):
            TEST_PIN.high();
            break;
        case cycle_fraction(9.25, 10):
            TEST_PIN.low();
            break;
        }
        break;
    }
}

static void updateOutput_D5(uint64_t tick, state_t state) {
    if (state.landing_light_active) {
        D5_PIN.high();
    } else {
        D5_PIN.low();
    }
}

static void updateOutput_D6(uint64_t tick, state_t state) {
    if (state.fly_state == FLYING) {
        switch (tick) {
            case 0:
                D6_PIN.high();
                break;
            case cycle_fraction(1, 70):
                D6_PIN.low();
                break;
            case cycle_fraction(2, 70):
                D6_PIN.high();
                break;
            case cycle_fraction(3, 70):
                D6_PIN.low();
                break;
            case cycle_fraction(4, 70):
                D6_PIN.high();
                break;
            case cycle_fraction(5, 70):
                D6_PIN.low();
                break;
            case cycle_fraction(6, 70):
                D6_PIN.high();
                break;
            case cycle_fraction(7, 70):
                D6_PIN.low();
                break;
            case cycle_fraction(8, 70):
                D6_PIN.high();
                break;
            case cycle_fraction(9, 70):
                D6_PIN.low();
                break;
            case cycle_fraction(10, 70):
                D6_PIN.high();
                break;
            case cycle_fraction(11, 70):
                D6_PIN.low();
                break;
            case cycle_fraction(5, 10):
                D6_PIN.high();
                break;
            case cycle_fraction(7.5, 10):
                D6_PIN.low();
                break;
        }
    } else if (state.fly_state == STANDBY) {
        if (tick < 500) {
            D6_PIN.high();
        } else {
            D6_PIN.low();
        }
    }
}

static void updateOutput_D8(uint64_t tick, state_t state) {
    switch(tick) {
        case 0:
            D8_PIN.high();
            break;
        case cycle_fraction(3, 10):
            D8_PIN.low();
            break;
        case cycle_fraction(6, 10):
            D8_PIN.high();
            break;
        case cycle_fraction(9, 10):
            D8_PIN.low();
            break;
    }
}

static void updateOutput_D9(uint64_t tick, state_t state) {
    switch(tick) {
        case 0:
            D9_PIN.low();
            break;
        case cycle_fraction(3, 10):
            D9_PIN.high();
            break;
        case cycle_fraction(6, 10):
            D9_PIN.low();
            break;
        case cycle_fraction(9, 10):
            D9_PIN.high();
            break;
    }
}

static void updateOutput_D10(uint64_t tick, state_t state) {
    switch(tick) {
        case 0:
            D10_PIN.high();
            break;
        case cycle_fraction(3, 10):
            D10_PIN.low();
            break;
        case cycle_fraction(6, 10):
            D10_PIN.high();
            break;
        case cycle_fraction(9, 10):
            D10_PIN.low();
            break;
    }
}

static void updateOutput_D11(uint64_t tick, state_t state) {
    switch(tick) {
        case 0:
            D11_PIN.low();
            break;
        case cycle_fraction(3, 10):
            D11_PIN.high();
            break;
        case cycle_fraction(6, 10):
            D11_PIN.low();
            break;
        case cycle_fraction(9, 10):
            D11_PIN.high();
            break;
    }
}

static void updateOutput_D14(uint64_t tick, state_t state) {
    switch(tick) {
        case 0:
            D14_PIN.high();
            break;
        case cycle_fraction(3, 10):
            D14_PIN.low();
            break;
        case cycle_fraction(6, 10):
            D14_PIN.high();
            break;
        case cycle_fraction(9, 10):
            D14_PIN.low();
            break;
    }
}

static void updateOutput_D15(uint64_t tick, state_t state) {
    switch(tick) {
        case 0:
            D15_PIN.low();
            break;
        case cycle_fraction(3, 10):
            D15_PIN.high();
            break;
        case cycle_fraction(6, 10):
            D15_PIN.low();
            break;
        case cycle_fraction(9, 10):
            D15_PIN.high();
            break;
    }
}

static void standby_channel_interrupt() {
    if (digitalRead(STANDBY_MODE_CHANNEL_PIN) == HIGH) {
        standby_channel_rise = micros();
    } else {
        standby_channel_pulse_time = micros() - standby_channel_rise;
    }
}

static void landing_channel_interrupt() {
    if (digitalRead(LANDING_LIGHT_CHANNEL_PIN) == HIGH) {
        landing_channel_rise = micros();
    } else {
        landing_channel_pulse_time = micros() - landing_channel_rise;
    }
}

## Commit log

2018-10-28 add board files
    [file5BCF4F82.sch, lighz.kicad_pcb, lighz.sch]
2018-10-28 update ignores to not ignore kicad lib files
2018-10-28 move microprocessor label silkscreen on PCB
    [lighz.kicad_pcb]
2018-10-28 add images of board
2018-10-29 add images of board to readme
2018-11-01 add pot, dbg pin
    [lighz.kicad_pcb, lighz.sch]
2018-11-04 remove const qualifier, it was wrong
    [blinkenlights.ino]
2018-11-04 remove possible data race
    write volatile variables only in interrupt
    read volatile variables only with disabled interrupts
2018-11-04 Add brake channel with PCInt
2018-11-04 pass state by reference, avoiding copy
    [blinkenlights.ino]
2018-11-05 add new board revision
    [file5BCF4F82.sch, lighz.kicad_pcb, lighz.sch]
2018-11-05 update images for new board revision
2018-11-05 millis instead of delay
2018-11-05 Add aux1/2 channels, fix PWM RC timeout
    [blinkenlights.ino]
2018-11-05 prevent possible race condition for staleness detection
    [blinkenlights.ino]
2018-11-05 Add pulse time short detection
    [blinkenlights.ino]
2018-11-17 update net names and add v1->v2 lipo jumper
    [file5BCF4F82.sch, lighz.kicad_pcb, lighz.sch]
2018-11-24 more realistic blink patterns
    and startup blink
    [file5BCF4F82.sch, lighz.kicad_pcb, lighz.sch]
2018-12-03 add voltage regulator (5V MCP1700)
    [file5BCF4F82.sch, lighz.kicad_pcb, lighz.sch]
2018-12-03 add capacitors for voltage regulator
    [file5BCF4F82.sch, lighz.kicad_pcb, lighz.sch]
2019-04-09 rev 3 move around labels
    [lighz.kicad_pcb]
2019-04-10 use analog pins for cooler leds
2019-04-10 currently deployed source
    ignore
2019-04-10 more switch statements
